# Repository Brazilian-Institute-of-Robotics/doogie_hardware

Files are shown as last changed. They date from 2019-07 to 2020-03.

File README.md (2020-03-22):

# Doogie Hardware
This repository is intend to gather all the files regarding the Doogie Mouse robot hardware and briefly explain about robot's electronic architecture.

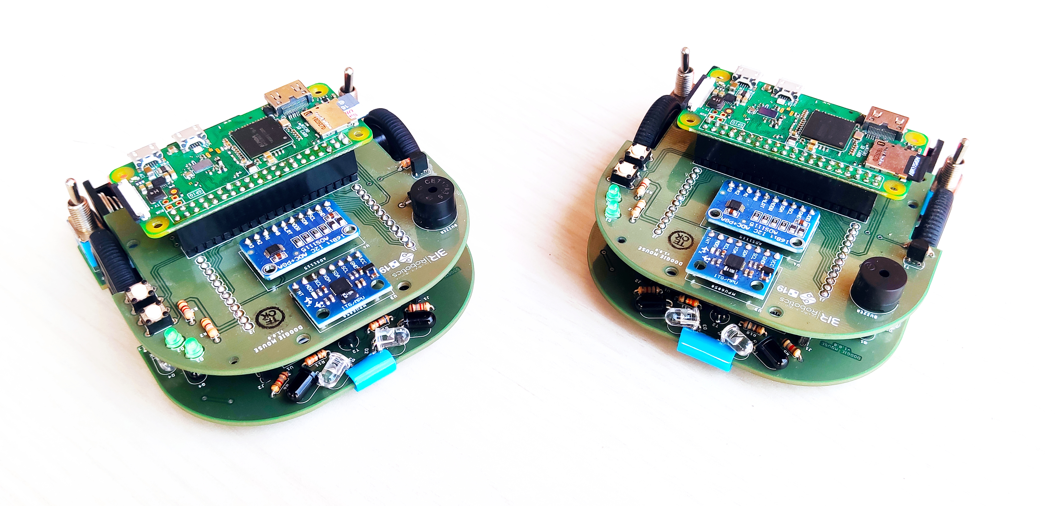
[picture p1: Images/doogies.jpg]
Doogie Photos


## Folder organization
- [Eagle]\: [Autocad Eagle] files (*.sch and *.brd) of top and bottom boards and a file used to check design rules (.dru)
- [Gerbers]\: Files used to manufacture the top and bottom boards
- [Libraries]\: Eagle libraries used in the layout of the Doogie Mouse robot boards
- [Schematics]\: Electronic schematics of top and bottom board in PDF format
- [BOM]\: Bill Of Materials

## Electronic architecture
The electronic architecture in the figure below demonstrates how Doogie Mousee components are electrically interconnected. For the purpose of better visualization, the voltage reference (Ground - GND) was omitted.

<p align="center">
<b>Figure 1: </b>Electronic architecture 
<br>
<br>
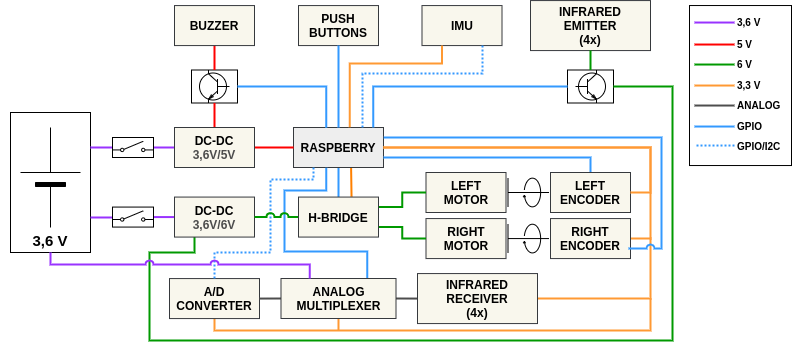
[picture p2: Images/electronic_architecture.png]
Electronic architecture

</p>

The Doogie is equipped with a Li-Ion battery with 3.6 V of nominal voltage. To make the battery voltage level compatible with the other components, two DC-DC converters are used. The first will supply 6 V exclusively for motors and emitting LEDs. The second is responsible for supplying the Raspberry Pi with 5 V. However, the components that are connected to the Raspberry Pi are powered by 3.3 V through an internal DC-DC converter on the microprocessor system board.

In order to facilitate the replication of the robot by users who want to use it, it was decided to use breakout boards, which are pre-assembled electronic boards. Doogie has six of them: two DC-DC voltage converters, an A/D converter, an IMU, an analog multiplexer and an H-Bridge. The other components, such as resistors, transistors, infrared LEDs, phototransistors and connectors, are soldered directly on the PCB.

Doogie components communicate and are controlled in several ways. The A/D converter and the IMU communicate with the Raspberry Pi via an I2C bus. As the specified A/D converter has only 4 channels (one for each infrared sensor), it was decided to use an analog multiplexer to allow the battery voltage value to be obtained as well. This multiplexer is controlled by digital pins from the processing unit. Finally, the control of the motors is performed by an H bridge with two independent channels. This power driver allows the directions of rotation of the motors to be controlled by digital pins from the Raspberry Pi while the speed control is performed by PWM.

For detailed description of components connections, see the electronic schematics [doogie_bottom_board](Schematics/doogie_bottom_board.pdf) and [doogie_top_board](Schematics/doogie_top_board.pdf).

## Boards overview
<p align="center">
<b>Top Board</b>
<br>
<br>
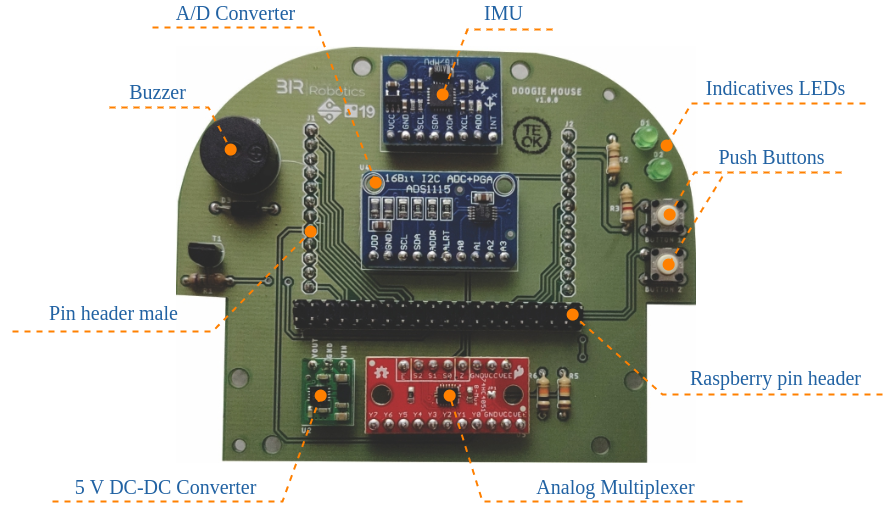
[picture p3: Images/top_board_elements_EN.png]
Top Board Components

</p>

<p align="center">
<b>Bottom Board</b>
<br>
<br>
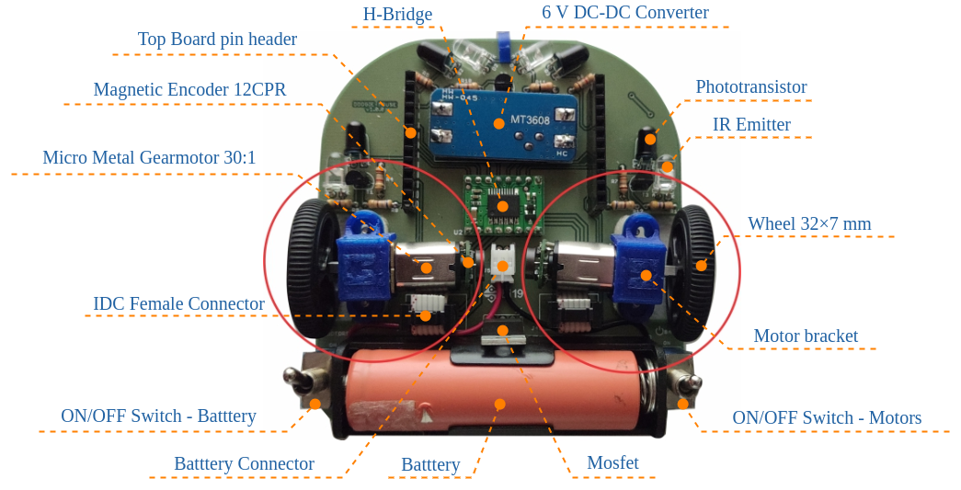
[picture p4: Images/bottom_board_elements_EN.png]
Bottom Board Components

</p>

## Assembly Instructions
See [Hardware Setup] on Doogie wiki page!

## Purpose of the Project

Doogie Mouse platform was originally developed in 2019 as an undergraduate thesis (Theoprax methodoly) at Centro Universitário SENAI CIMATEC in partnership with Brazillian Institute of Robotics, for teaching principles of artificial intelligence using high level framework for writing and reusing robot software.

It's a open source project and expects modifications and contributions from it's users. 

## Change Log
#### [1.0] - 2019-12-10
- First version

## Bugs & Feature Requests
Please report bugs and request features using the [Issue Tracker](https://github.com/Brazilian-Institute-of-Robotics/doogie_hardware/issues).

[Eagle]: https://github.com/Brazilian-Institute-of-Robotics/doogie_hardware/tree/master/Eagle
[Autocad Eagle]: https://www.autodesk.com/products/eagle/overview?geoNavigationPreferredSite=US
[Gerbers]: https://github.com/Brazilian-Institute-of-Robotics/doogie_hardware/tree/master/Gerbers
[Libraries]: https://github.com/Brazilian-Institute-of-Robotics/doogie_hardware/tree/master/Libraries
[Schematics]: https://github.com/Brazilian-Institute-of-Robotics/doogie_hardware/tree/master/Schematics
[BOM]: https://github.com/Brazilian-Institute-of-Robotics/doogie_hardware/tree/master/BOM
[Hardware Setup]: https://github.com/Brazilian-Institute-of-Robotics/doogie/wiki/Hardware-Setup

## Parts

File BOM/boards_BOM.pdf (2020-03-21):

DOOGIE TOP BOARD - BOM

Qty | Value | Device | Package | Parts | Description
2 | | CONN_12 | 1X12 | J1, J2 | Multi connection point. Often used as Generic Header-pin footprint for 0.1 inch spaced/style header connections
2 | 10k | R-EU_0204/7 | 0204/7 | R5, R6 | RESISTOR, European symbol
1 | 1N4004 | 1N4004 | DO41-10 | D3 | DIODE
1 | 390R | R-EU_0204/7 | 0204/7 | R2 | RESISTOR, European symbol
1 | 74HC4051_SPARKFUN | 74HC4051_SPARKFUN | 74HC4051_SPARKFUN | U5
1 | 750R | R-EU_0204/7 | 0204/7 | R1 | RESISTOR, European symbol
1 | 820R | R-EU_0204/7 | 0204/7 | R3 | RESISTOR, European symbol
1 | ADC-4CH-ADS1115 | ADC-4CH-ADS1115 | ADC-4CH-ADS1115 | U4 | 4 Channel 16-Bit Analog-to-Digital Converter based on ADS1115 chip
1 | BC337 | BC337 | TO92 | T1 | NPN TRANSISTOR
1 | F/TMB | F/TMB | F/TMB | BUZZER | BUZZER Source: Buerklin
2 | GREEN | LED3MM | LED_3MM | D1, D2 | LED (Generic)
1 | GY-521MPU6050 | GY-521MPU6050 | GY-521 | U3
2MOMENTARY-SWITCH-SPST-PTH-6.0MM MOMENTARY-SWITCH-SPST-PTH-6.0MM TACTILE_SWITCH_PTH_6.0MM | | | | S1, S2 | Momentary Switch (Pushbutton) - SPST
1 | RPI-ZERO | RPI-ZERO | | U1
1 | U1V10F5 | U1V10F5 | U1V10F5 | U2 | Pololu 5V Step-Up Voltage Regulator U1V10F5

DOOGIE BOTTOM BOARD - BOM

Qty | Value | Device | Package | Parts | Description
1 | | CONN_02JST-PTH-2 | JST-2-PTH | J5 | Multi connection point. Often used as Generic Header-pin footprint for 0.1 inch spaced/style header connections
2 | | CONN_03X2SHROUD | 2X3-SHROUDED | J3, J4 | Multi connection point. Often used as Generic Header-pin footprint for 0.1 inch spaced/style header connections
2 | | CONN_12 | 1X12 | J1, J2 | Multi connection point. Often used as Generic Header-pin footprint for 0.1 inch spaced/style header connections
2 | | M9040P | M9040P | S1, S2 | TOGGLE SWITCH
4 | 1k8 | R-EU_0204/7 | 0204/7 | R4, R5, R6, R7 | RESISTOR, European symbol
1 | 33R | R-EU_0204/7 | 0204/7 | R11 | RESISTOR, European symbol
2 | 47R | R-EU_0204/7 | 0204/7 | R9, R13 | RESISTOR, European symbol
3 | 680R | R-EU_0204/7 | 0204/7 | R8, R10, R12 | RESISTOR, European symbol
1 | BATTERY_HOLDER | BATTERY_HOLDER | BATTERY_HOLDER | BATTERY_HOLDER
3 | BC337 | BC337 | TO92 | T1, T2, T3 | NPN TRANSISTOR
1 | DC-DC-STEP-UP-MT3608 | DC-DC-STEP-UP-MT3608 | DC-DC-STEP-UP-MT3608 | U1 | DC/DC Step-Up Regulator based on MT3608 chip
1 | IRF9530 | IRF9530 | TO220BV | Q6 | P-CHANNEL HEXFET POWER-MOS-FET
4 | SFH4545 | SFH4545 | SFH4545-AK | D1, D2, D3, D4
1 | TB6612FNG | TB6612FNG | TB6612FNG | U2 | TB6612FNG Dual Motor Driver Carrier
4 | TEFT4300 | TEFT4300_5MM_RA | TEFT_5MM_RA | Q1, Q2, Q3, Q4 | TEFT4300

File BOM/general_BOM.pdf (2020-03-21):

Top Board
Item | Component | Qty. | Description
1 | Printed Circuit Board | 1 | doogie_top_board
2 | Raspberry Pi | 1 | Raspberry Pi Zero W
3 | Micro Sd | 1 | Memory Card microSD 16GB Class 10 SanDisk
4 | Voltage Regulator | 1 | 5V voltage regulator Pololu Step-Up U1V10F5
5 | Imu | 1 | 3 axes accelerometer and gyro 6-DOF MPU 6050
6 | A / D Converter | 1 | Analog Digital Converter channels 4 ADS1115
7 | Analog Multiplexer | 1 | Module Multiplexers 74HC4051 8 channels Sparkfun
8 | Pin Male Bar 1X12 | 1 | Pin bar 1×40 180º 20mm
9 | Pin Bar Male 2X40 | 1 | Pin bar 2×40 180º
10 | Pin Female Bar 2X20 | 1 | Pin Bar 2 × 20 Male And Female
10 | Push Button | 2 | Key Touch Push-Button
11 | Led | 2 | 3mm LEDs
12 | Buzzer | 1 | Active buzzer 5V
13 | Transistor | 1 | NPN transistor BC337
14 | Diode | 1 | Rectifier diode 1N4007
15 | Resistor | 1 | Resistor 750Ω 1 / 4W
16 | Resistor | 1 | Resistor 390Ω 1 / 4W
17 | Resistor | 1 | Resistor 820Ω 1 / 4W
18 | Resistor | 2 | Resistor 10k 1 / 4W

Bottom Board
Item | Component | Qty. | Description
1 | Printed Circuit Board | 1 | doogie_bottom_board
2 | Voltage Regulator | 1 | Boost Converter DC Adjustable Step Up
3 | H Bridge | 1 | TB6612FNG Dual Motor Driver Carrier
4 | Pin Female Bar 1X12 | 1 | Pins bar 1 × 40 Female 180º
5 | Pin Male Bar 2X3 | 2 | Pin bar 180º 2 x 40 (used on the board top)
6 | Connector | 1 | Connector JST XH male wrapped
7 | 3 Terminals Switch | 2 | Switch 3 Terminals Toggle Switch SPDT
8 | Phototransistor | 4 | Infrared Phototransistor 5mm IR receiver
9 | Infrared Emitter | 4 | Infrared IR transmitter LED 5mm
10 | Transistor | 3 | NPN transistor BC337
11 | Mosfet | 1 | P-Channel MOSFET TO220 IRF4905
12 | Resistor | 1 | Resistor 33Ω 1 / 4W
13 | Resistor | 2 | Resistor 47Ω 1 / 4W
14 | Resistor | 3 | Resistor 680Ω 1 / 4W
15 | Resistor | 4 | Resistor 1k8Ω 1 / 4W
16 | Motor | 2 | 30: 1 Micro Metal Gearmotor HP 6V motor shaft extended
17 | Pair Of Magnetic Encoder | 1 | Pair of magnetic metal micro motor encoder Gearmotors, 12 CPR 2.7-18V
18 | Pair Of Wheels | 1 | Pololu wheel pair 32 × 7mm
19 | Par Motor Brackets | 1 | Motor Bracket - 3D Printing
20 | IDC Female connector | 2 | IDC female connector - 6-way
21 | Flat Cable | 1 | Flat Cable - 6 parts (1m)
22 | Battery | 1 | Li-Ion 18650 3.7V 2200mAh 2C
23 | Support For Battery | 1 | Support for battery 18650

Auxiliaries
Item | Component | Qty. | Description
1 | USB/Micro USB Adapter | 2 | Cable USB to Micro USB
2 | HDMI/Mini HDMI Adapter | 1 | HDMI Female Adapter Mini HDMI Male

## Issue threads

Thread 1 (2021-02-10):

Fix small errors on the board first version

mateusmenezes95, 2021-02-10:
After the assembly and test with the first version of the doogie boards, some points were listed to be fixed in the next versions. Below are the point with some comments.

- **Inverter DC-DC of the motors:** In the assembly process of the bottom board, it was noticed the pads of the motors' DC-DC converter were inverted. The solution was to put the DC-DC head down. Then it's necessary to fix this issue in the next versions.
- **Drill the key holes:** It's necessary to increase the diameter of ON/OFF key holes pads because in the first version the diameter no fit with the key pins.
- **Reverse silk ON / OFF of the ON/OFF keys:** In the current verison putting the key lever on OFF position turn on the robot and putting in ON position, turn off. This issue could be solved just by inverting the silk on the bottom board.
- **Place the silk on the power LEDs:** The top board has two LEDs to indicate when power and the logical circuit are turned on. However, there is no indication on the board to inform which LED is related to the power circuit and which LED is related to the logical circuit.
- **Put I2C address in ADS1115 (Connect ADDR in GND):** It's necessary to connect the ADDR pin of ADS1115 to GND to assign it an I2C address. In the current version, this connection was made by wire.
- **Place test points:** For hardware debug purposes it's nice to put point test points on the boards to evaluate voltage levels and signal. It's a good practice in PCB development.
- **Increase the space where the wheels are by 2mm:** It's necessary to increase the space where the wheels are to avoid the tires touch on the board edges.
- **Place capacitors in parallel with the emitters for the use of current peaks:** Put the capacitor to provide high peak current in small intervals. With this approach, the resolution of the sensor is improved. This a common technique used in micromouse robots.
- **Change Buzzer's GPIO:** The buzzer it's not working well because like seems the pin used to control it is connected with another function in the board. It's important to do tests before choose a new pin.
- **Connect the interruption pin of the MPU6050:** It's nice to connect the interruption pin of the IMU to one pin of the raspberry to enjoy the interruption functionalities of the MPU6050 device.

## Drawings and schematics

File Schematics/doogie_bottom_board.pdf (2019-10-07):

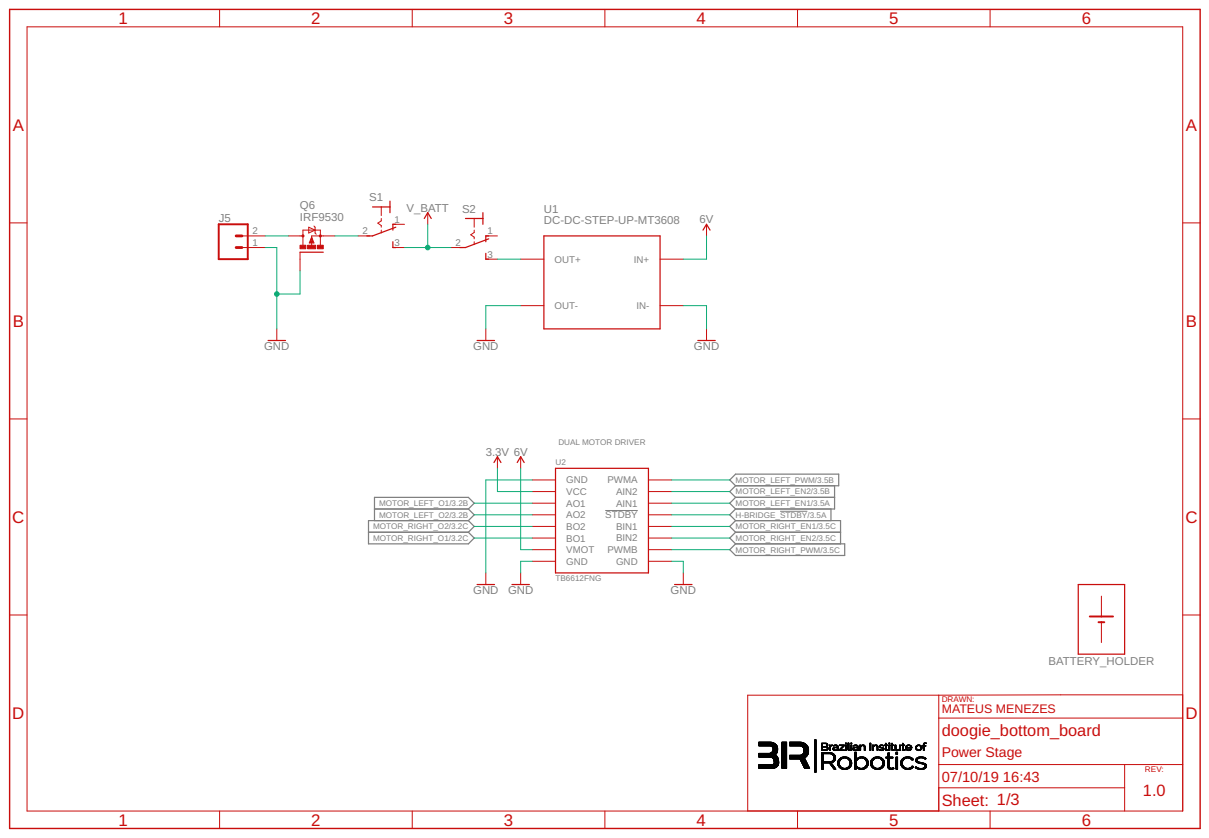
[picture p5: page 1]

DC-DC-STEP-UP-MT3608

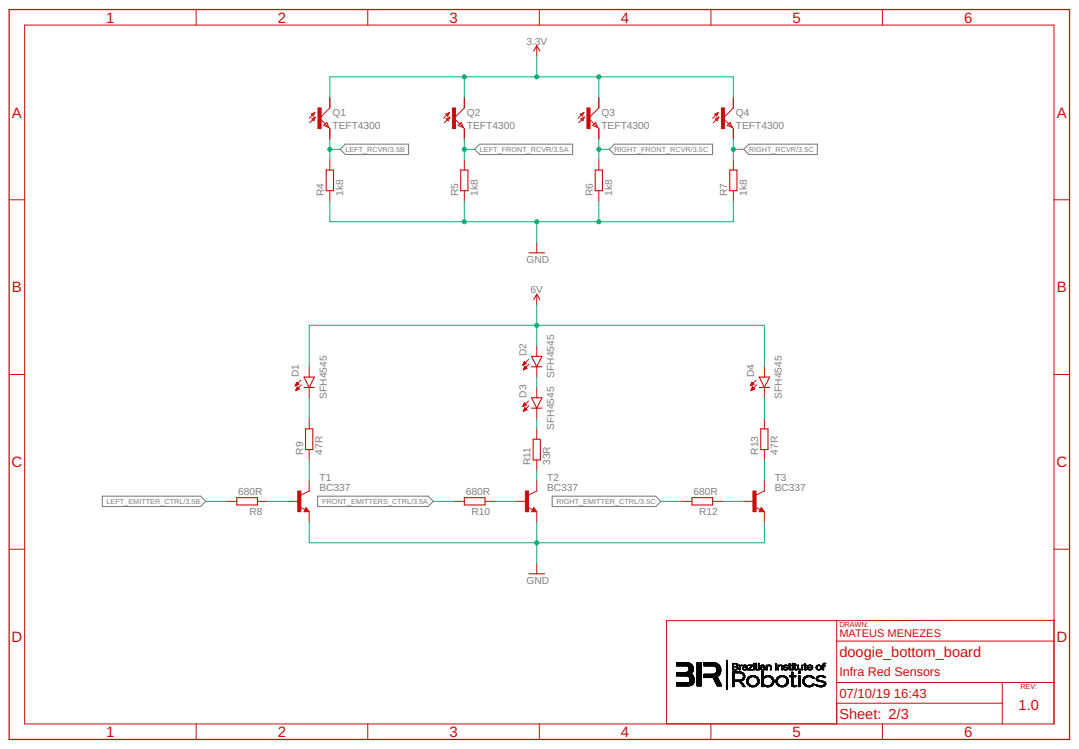
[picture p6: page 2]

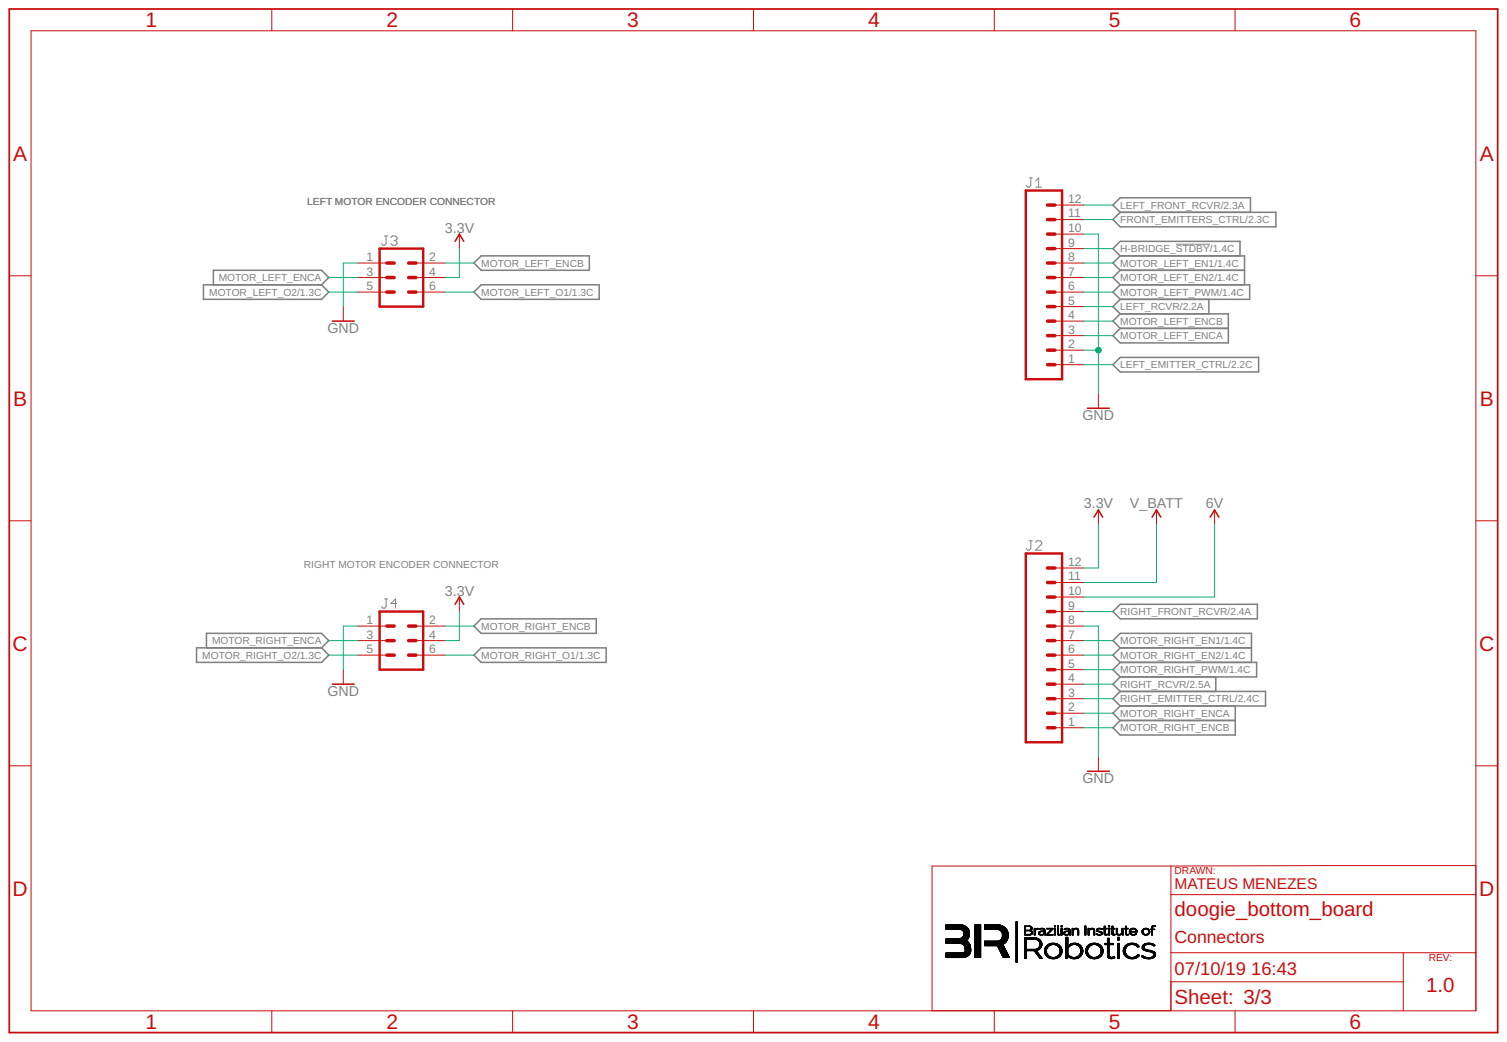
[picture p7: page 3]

LEFT MOTOR ENCODER CONNECTOR

LEFT MOTOR ENCODER CONNECTOR 3.3V

RIGHT MOTOR ENCODER CONNECTOR

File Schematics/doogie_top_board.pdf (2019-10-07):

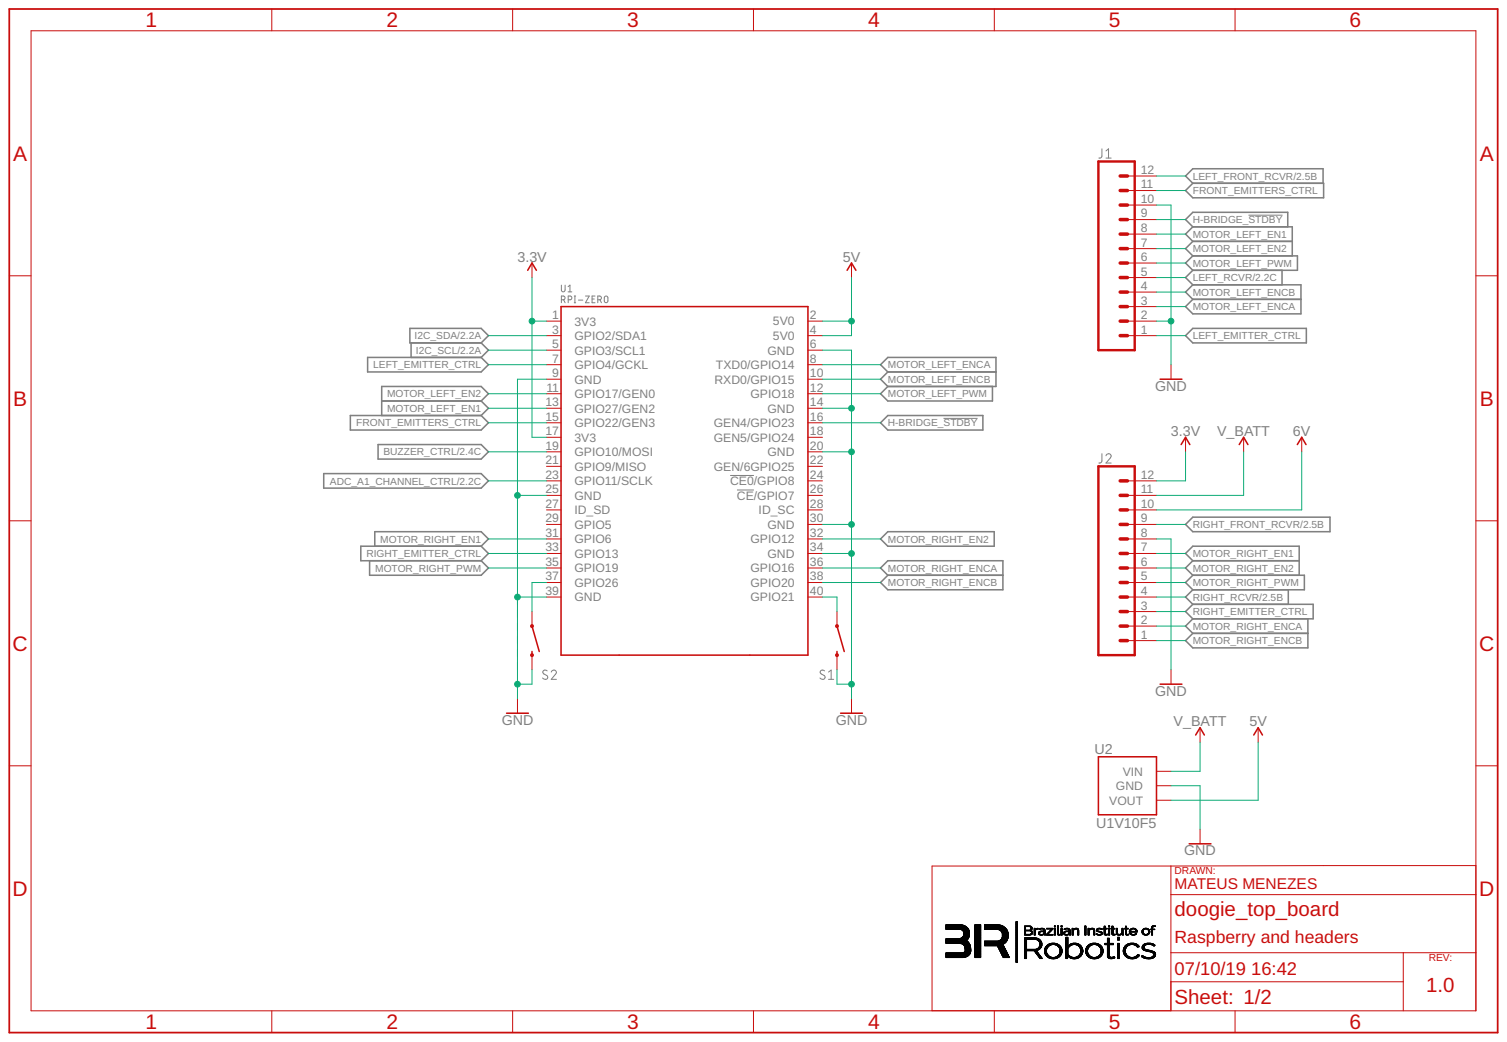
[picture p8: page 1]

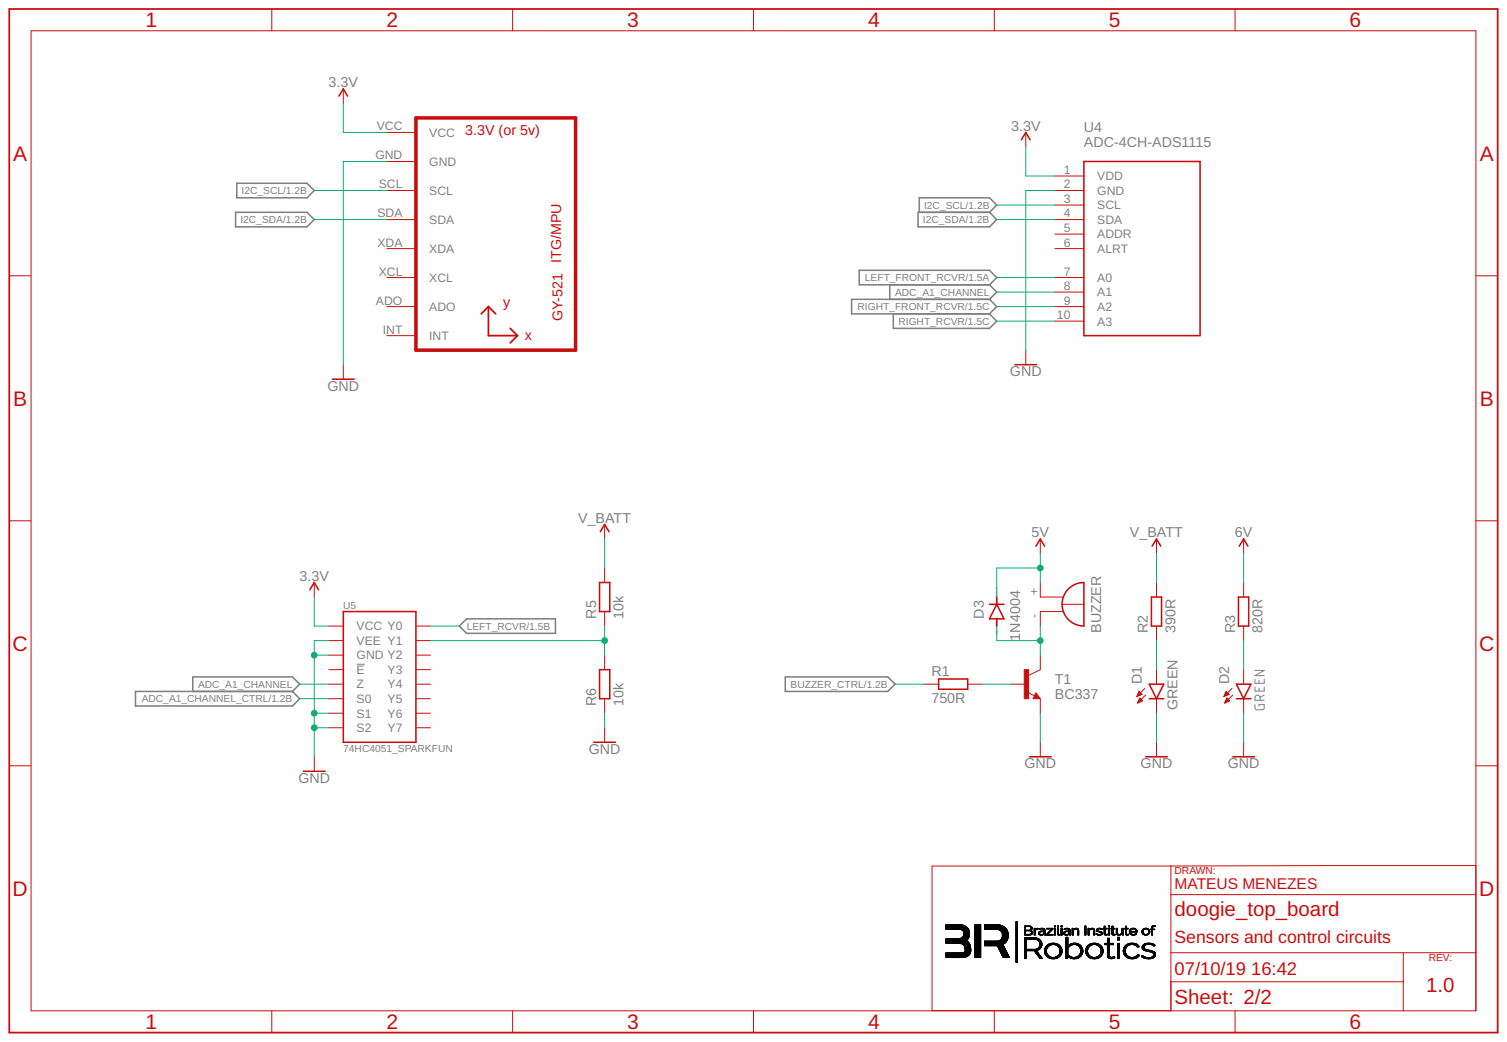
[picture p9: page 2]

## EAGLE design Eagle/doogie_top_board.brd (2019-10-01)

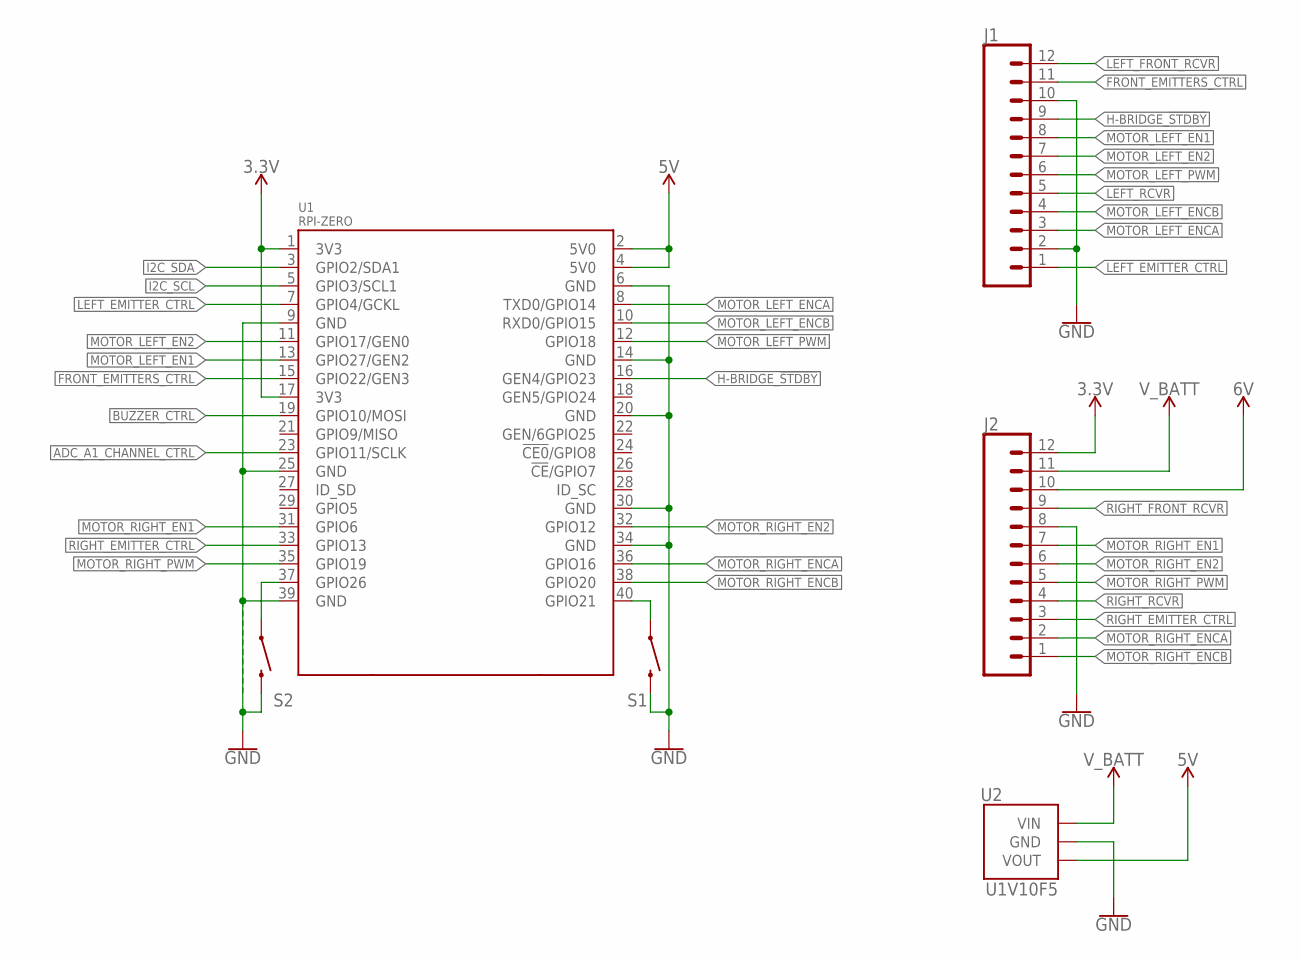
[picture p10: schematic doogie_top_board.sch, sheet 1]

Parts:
J1, J2: CONN_12; 1X12
S1, S2: MOMENTARY-SWITCH-SPST-PTH-6.0MM; TACTILE_SWITCH_PTH_6.0MM
U1: RPI-ZERO; RASPBERRYPI_BASTELSTUBE_V13_RASPI_BOARD_B+_FULL
U2: U1V10F5

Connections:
3.3V: J2.12, U1.1 (3V3), U1.17 (3V3); also elsewhere on the board
5V: U1.2 (5V0), U1.4 (5V0), U2.VOUT; also elsewhere on the board
ADC_A1_CHANNEL_CTRL: U1.23 (GPIO11/SCLK); also elsewhere on the board
BUZZER_CTRL: U1.19 (GPIO10/MOSI); also elsewhere on the board
FRONT_EMITTERS_CTRL: J1.11, U1.15 (GPIO22/GEN3)
GND: J1.2, J1.10, J2.8, S1.3 (2), S2.3 (2), U1.6 (GND), U1.9 (GND), U1.14 (GND), U1.20 (GND), U1.25 (GND), U1.30 (GND), U1.34 (GND), U1.39 (GND), U2.GND; also elsewhere on the board
H-BRIDGE_!STDBY: J1.9, U1.16 (GEN4/GPIO23)
I2C_SCL: U1.5 (GPIO3/SCL1); also elsewhere on the board
I2C_SDA: U1.3 (GPIO2/SDA1); also elsewhere on the board
LEFT_EMITTER_CTRL: J1.1, U1.7 (GPIO4/GCKL)
LEFT_FRONT_RCVR: J1.12; also elsewhere on the board
LEFT_RCVR: J1.5; also elsewhere on the board
MOTOR_LEFT_EN1: J1.8, U1.13 (GPIO27/GEN2)
MOTOR_LEFT_EN2: J1.7, U1.11 (GPIO17/GEN0)
MOTOR_LEFT_ENCA: J1.3, U1.8 (TXD0/GPIO14)
MOTOR_LEFT_ENCB: J1.4, U1.10 (RXD0/GPIO15)
MOTOR_LEFT_PWM: J1.6, U1.12 (GPIO18)
MOTOR_RIGHT_EN1: J2.7, U1.31 (GPIO6)
MOTOR_RIGHT_EN2: J2.6, U1.32 (GPIO12)
MOTOR_RIGHT_ENCA: J2.2, U1.36 (GPIO16)
MOTOR_RIGHT_ENCB: J2.1, U1.38 (GPIO20)
MOTOR_RIGHT_PWM: J2.5, U1.35 (GPIO19)
unnamed: S2.1, U1.37 (GPIO26)
unnamed: S1.1, U1.40 (GPIO21)
RIGHT_EMITTER_CTRL: J2.3, U1.33 (GPIO13)
RIGHT_FRONT_RCVR: J2.9; also elsewhere on the board
RIGHT_RCVR: J2.4; also elsewhere on the board
VOUT: J2.10; also elsewhere on the board
V_BATT: J2.11, U2.VIN; also elsewhere on the board

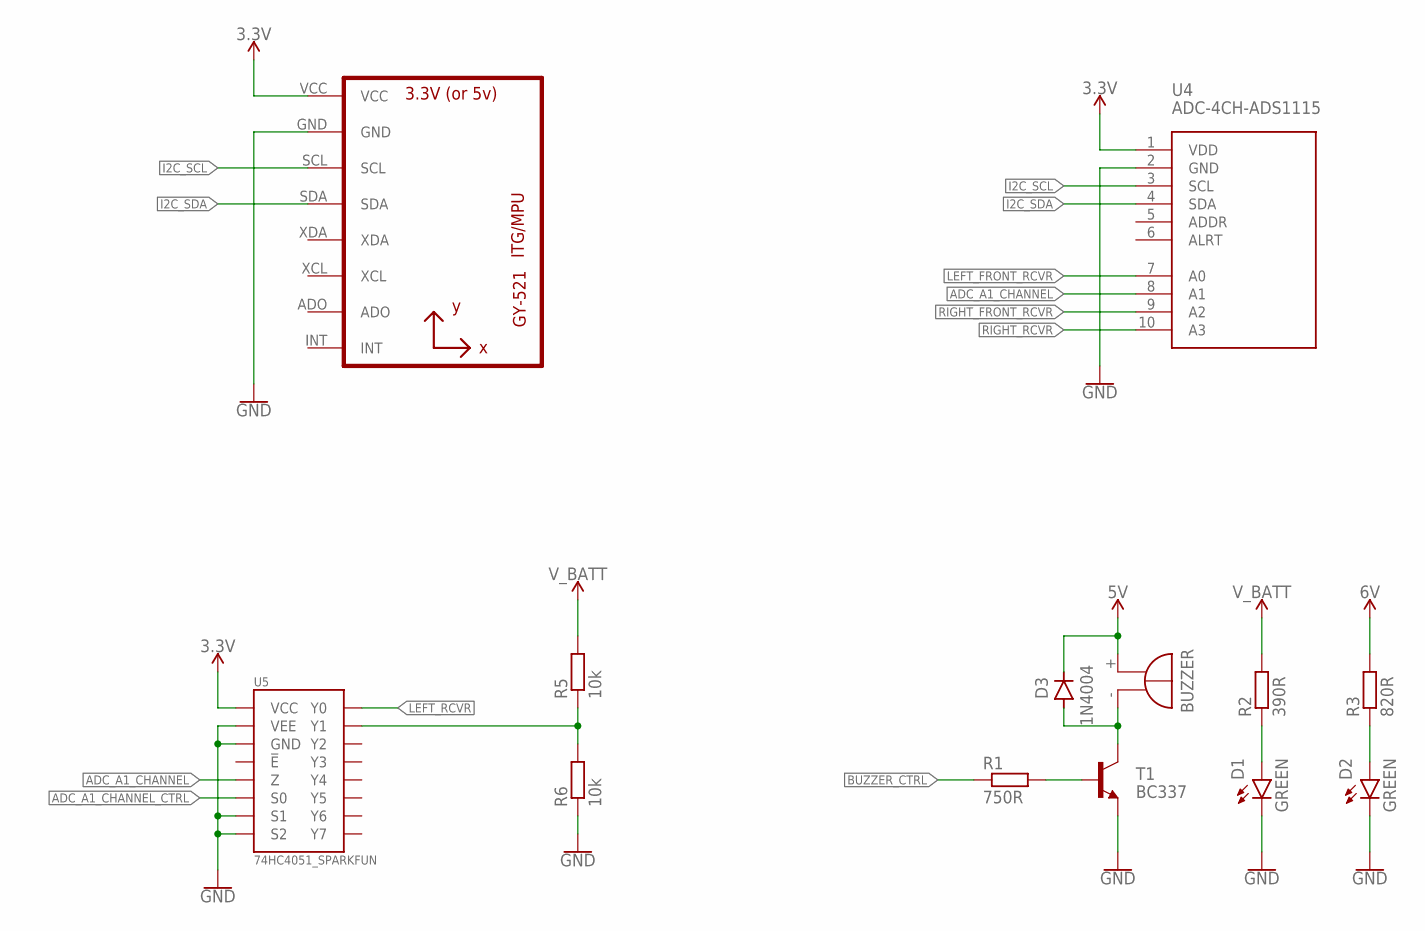
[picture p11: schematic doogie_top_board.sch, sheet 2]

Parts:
BUZZER: F/TMB
D1, D2: GREEN; LED_3MM
D3: 1N4004; DO41-10
R1: 750R; 0204/7
R2: 390R; 0204/7
R3: 820R; 0204/7
R5, R6: 10k; 0204/7
T1: BC337; TO92
U3: GY-521MPU6050; GY-521
U4: ADC-4CH-ADS1115
U5: 74HC4051_SPARKFUN

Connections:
3.3V: U3.VCC, U4.1 (VDD), U5.VCC, U5.VCC@1 (VCC); also elsewhere on the board
5V: BUZZER.+, D3.C; also elsewhere on the board
ADC_A1_CHANNEL: U4.8 (A1), U5.Z
ADC_A1_CHANNEL_CTRL: U5.S0; also elsewhere on the board
BUZZER_CTRL: R1.1; also elsewhere on the board
GND: D1.K (C), D2.K (C), R6.1, T1.1 (E), U3.GND, U4.2 (GND), U5.GND, U5.GND@1 (GND), U5.S1, U5.S2, U5.VEE, U5.VEE@1 (VEE); also elsewhere on the board
I2C_SCL: U3.SCL, U4.3 (SCL); also elsewhere on the board
I2C_SDA: U3.SDA, U4.4 (SDA); also elsewhere on the board
LEFT_FRONT_RCVR: U4.7 (A0); also elsewhere on the board
LEFT_RCVR: U5.Y0; also elsewhere on the board
unnamed: BUZZER.-, D3.A, T1.3 (C)
unnamed: R1.2, T1.2 (B)
unnamed: D1.A, R2.1
unnamed: D2.A, R3.1
unnamed: R5.1, R6.2, U5.Y1
RIGHT_FRONT_RCVR: U4.9 (A2); also elsewhere on the board
RIGHT_RCVR: U4.10 (A3); also elsewhere on the board
VOUT: R3.2; also elsewhere on the board
V_BATT: R2.2, R5.2; also elsewhere on the board

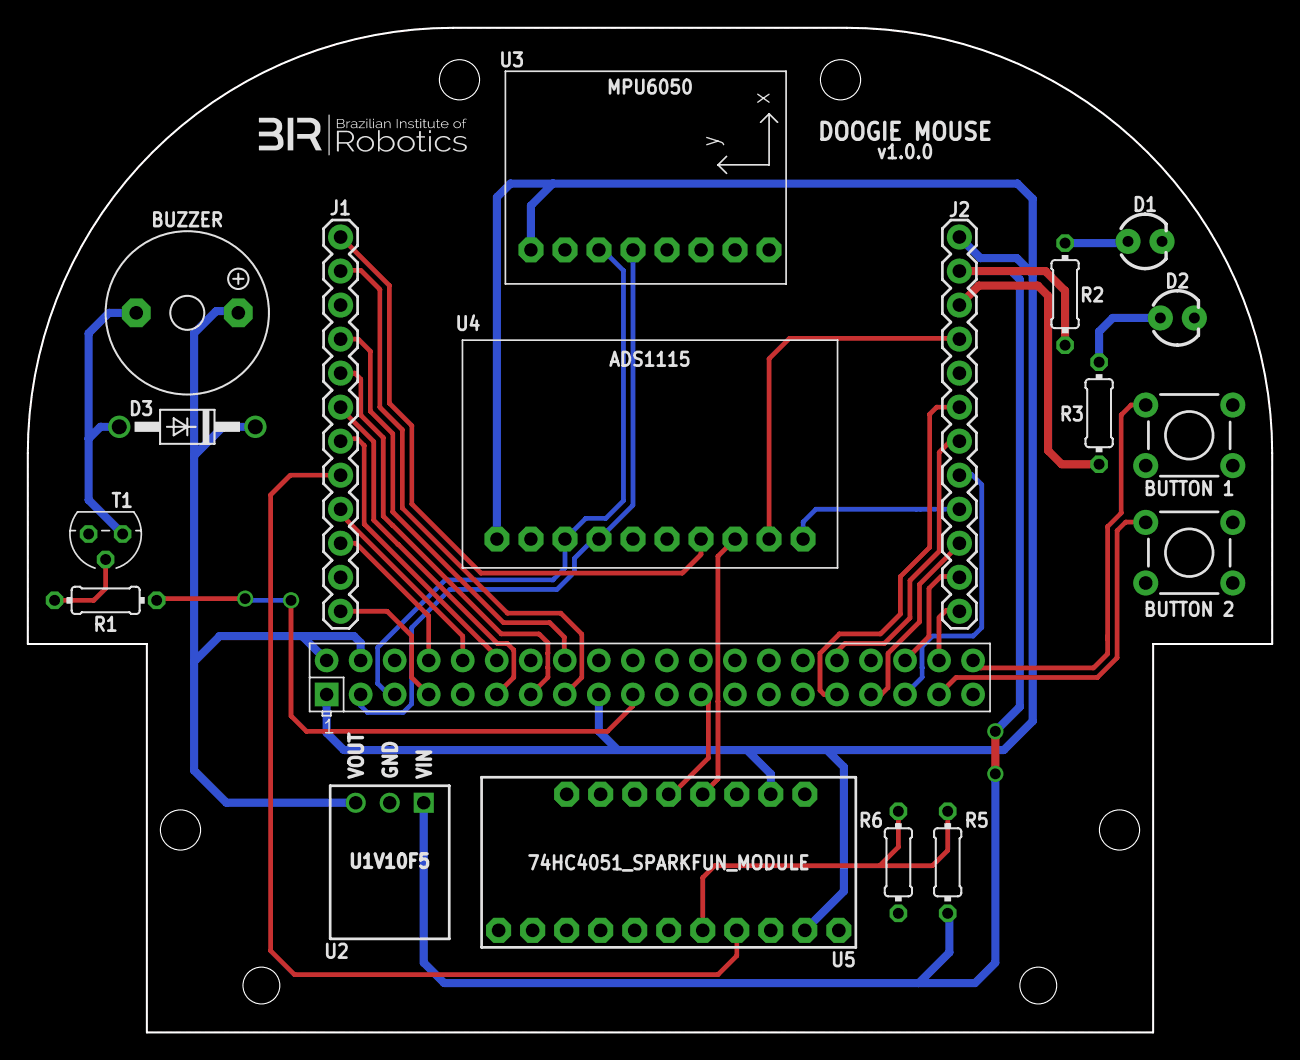
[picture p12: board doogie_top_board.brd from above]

Board: 2 copper layers, 92.9 x 75.0 mm, 19 parts (0 on the bottom side), 35 nets.

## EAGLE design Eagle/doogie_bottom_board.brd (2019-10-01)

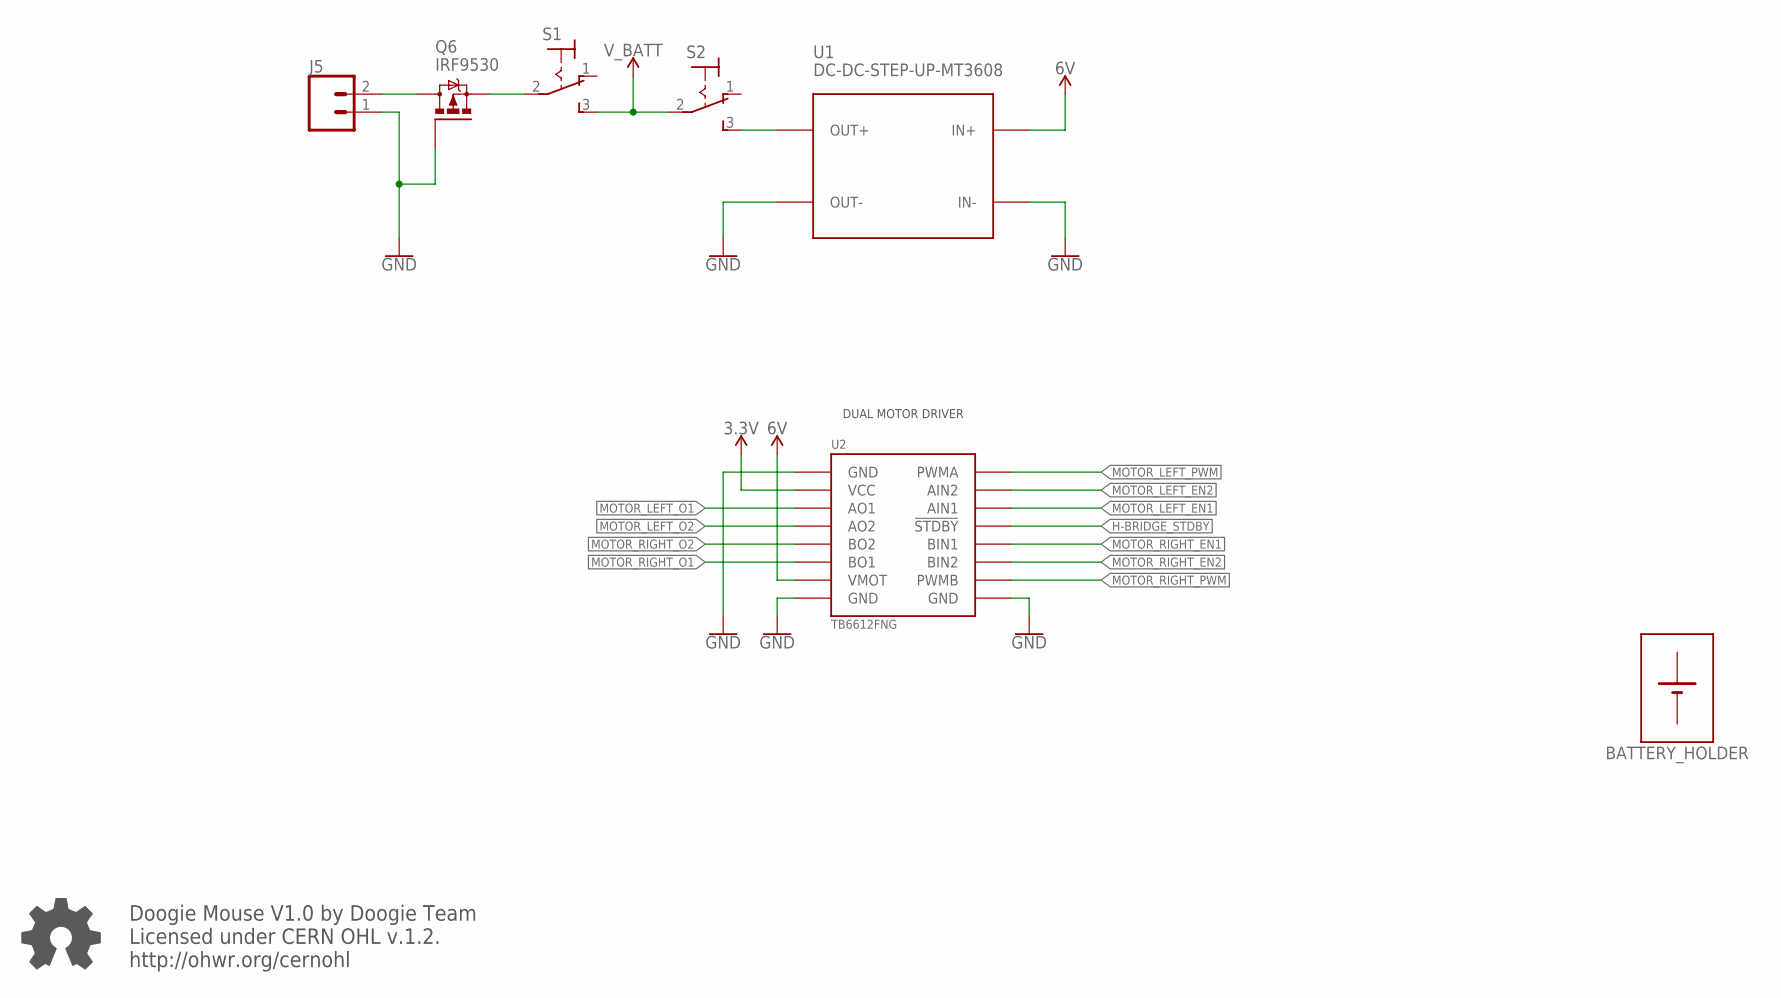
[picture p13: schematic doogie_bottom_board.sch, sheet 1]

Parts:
BATTERY_HOLDER: BATTERY_HOLDER
J5: CONN_02JST-PTH-2; JST-2-PTH
Q6: IRF9530; TO220BV
S1, S2: M9040P
U1: DC-DC-STEP-UP-MT3608
U2: TB6612FNG

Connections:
3.3V: U2.2 (VCC); also elsewhere on the board
6V: U1.IN+, U2.7 (VMOT); also elsewhere on the board
FILLING_POLYGON: J5.1, Q6.G, U1.IN-, U1.OUT-, U2.1 (GND), U2.8 (GND), U2.16 (GND); also elsewhere on the board
H-BRIDGE_!STDBY: U2.12 (!STDBY!); also elsewhere on the board
MOTOR_LEFT_EN1: U2.11 (AIN1); also elsewhere on the board
MOTOR_LEFT_EN2: U2.10 (AIN2); also elsewhere on the board
MOTOR_LEFT_O1: U2.3 (AO1); also elsewhere on the board
MOTOR_LEFT_O2: U2.4 (AO2); also elsewhere on the board
MOTOR_LEFT_PWM: U2.9 (PWMA); also elsewhere on the board
MOTOR_RIGHT_EN1: U2.13 (BIN1); also elsewhere on the board
MOTOR_RIGHT_EN2: U2.14 (BIN2); also elsewhere on the board
MOTOR_RIGHT_O1: U2.6 (BO1); also elsewhere on the board
MOTOR_RIGHT_O2: U2.5 (BO2); also elsewhere on the board
MOTOR_RIGHT_PWM: U2.15 (PWMB); also elsewhere on the board
unnamed: S2.3 (S), U1.OUT+
unnamed: J5.2, Q6.D
unnamed: Q6.S, S1.2
V_BATT: S1.3 (S), S2.2; also elsewhere on the board

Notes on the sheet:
Doogie Mouse V1.0 by Doogie Team Licensed under CERN OHL v.1.2. http://ohwr.org/cernohl
DUAL MOTOR DRIVER

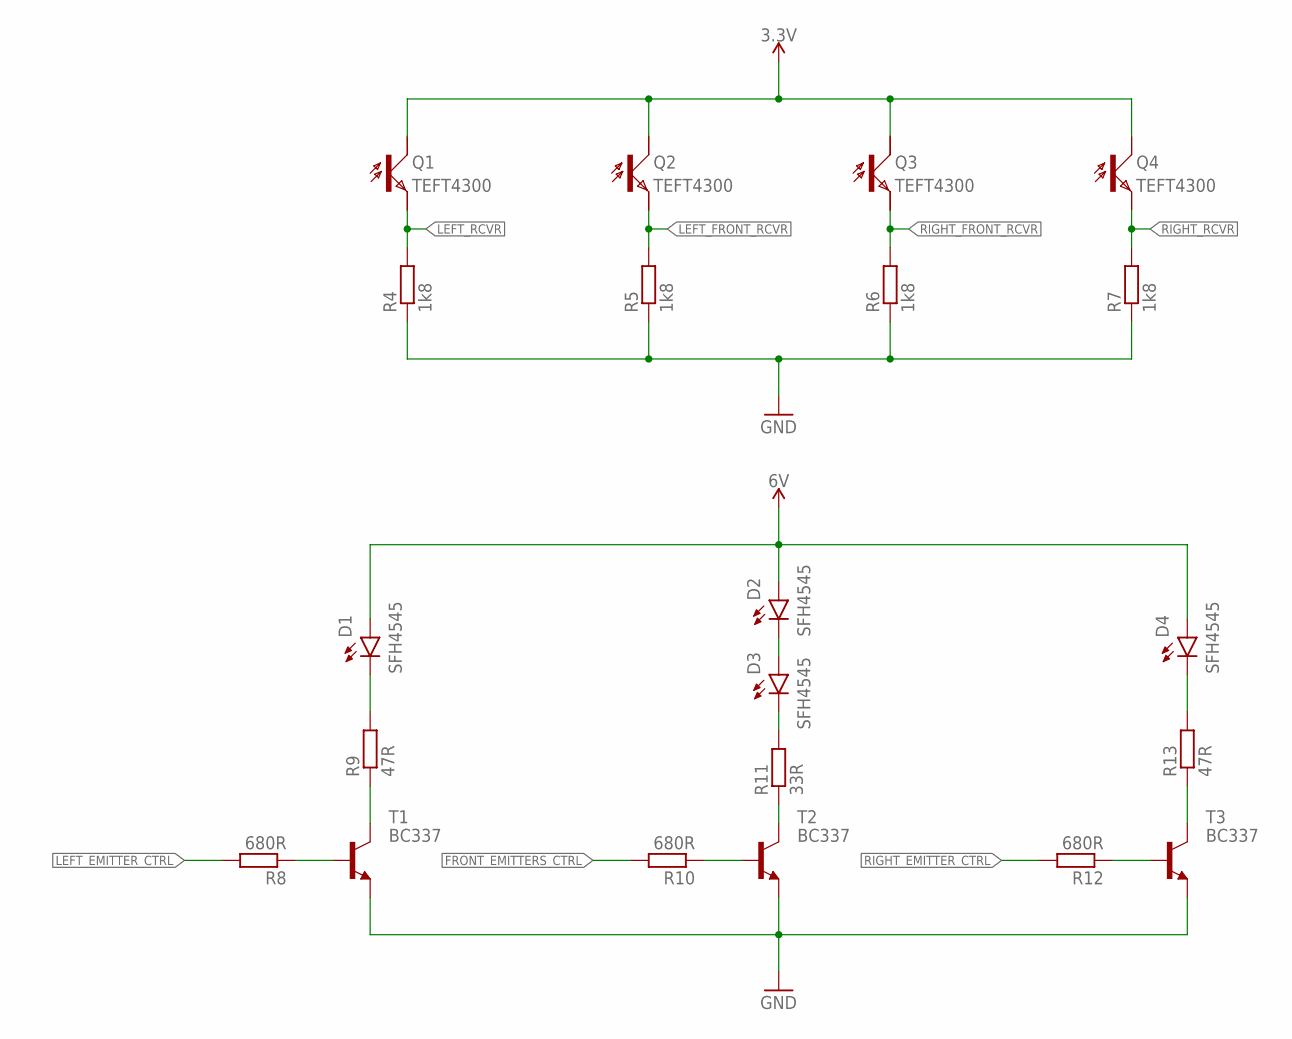
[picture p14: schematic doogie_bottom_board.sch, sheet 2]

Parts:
D1, D2, D3, D4: SFH4545; SFH4545-AK
Q1, Q2, Q3, Q4: TEFT4300; TEFT_5MM_RA
R4, R5, R6, R7: 1k8; 0204/7
R8, R10, R12: 680R; 0204/7
R9, R13: 47R; 0204/7
R11: 33R; 0204/7
T1, T2, T3: BC337; TO92

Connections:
3.3V: Q1.C, Q2.C, Q3.C, Q4.C; also elsewhere on the board
6V: D1.A, D2.A, D4.A; also elsewhere on the board
FILLING_POLYGON: R4.1, R5.1, R6.1, R7.1, T1.1 (E), T2.1 (E), T3.1 (E); also elsewhere on the board
FRONT_EMITTERS_CTRL: R10.2; also elsewhere on the board
LEFT_EMITTER_CTRL: R8.2; also elsewhere on the board
LEFT_FRONT_RCVR: Q2.E, R5.2; also elsewhere on the board
LEFT_RCVR: Q1.E, R4.2; also elsewhere on the board
unnamed: R9.1, T1.3 (C)
unnamed: R11.1, T2.3 (C)
unnamed: R13.1, T3.3 (C)
unnamed: R8.1, T1.2 (B)
unnamed: R10.1, T2.2 (B)
unnamed: R12.1, T3.2 (B)
unnamed: D2.K (C), D3.A
unnamed: D1.K (C), R9.2
unnamed: D4.K (C), R13.2
unnamed: D3.K (C), R11.2
RIGHT_EMITTER_CTRL: R12.2; also elsewhere on the board
RIGHT_FRONT_RCVR: Q3.E, R6.2; also elsewhere on the board
RIGHT_RCVR: Q4.E, R7.2; also elsewhere on the board

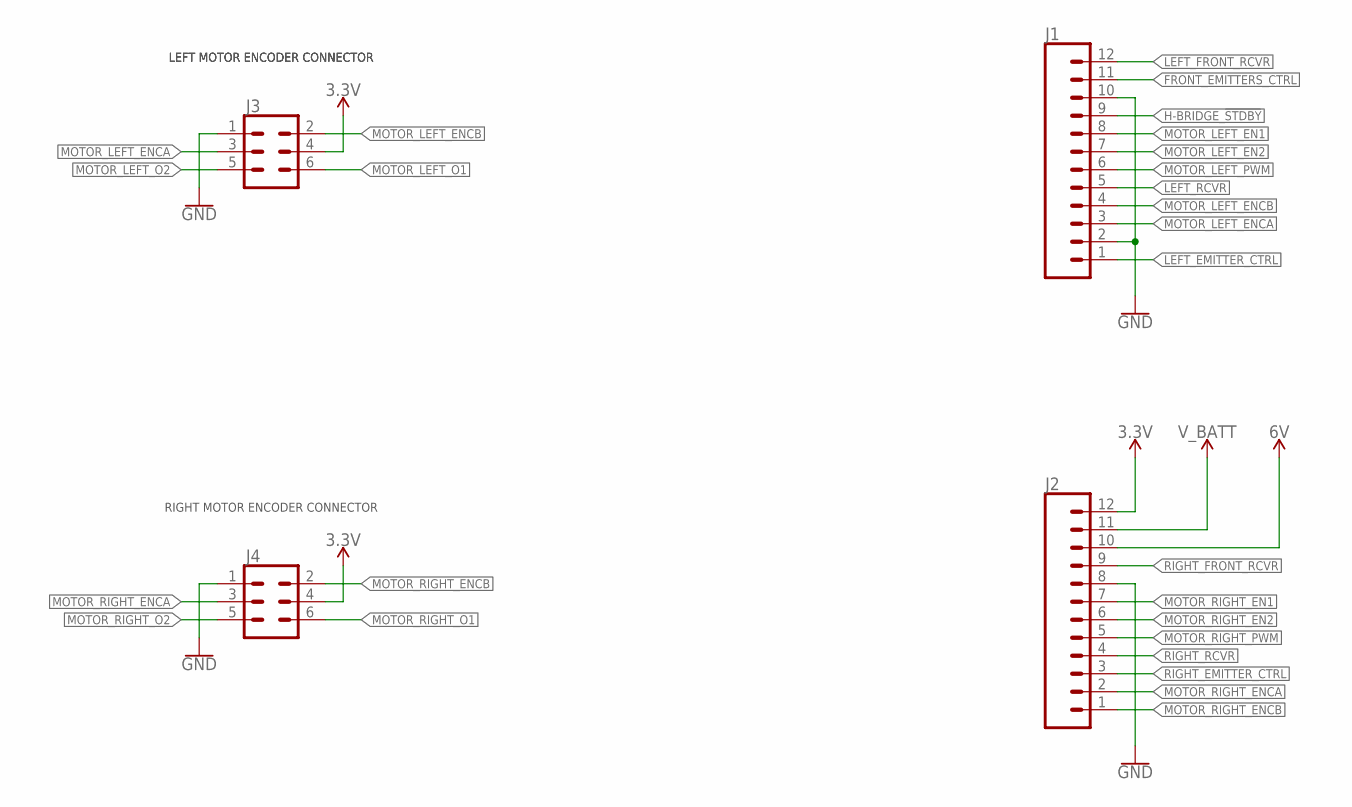
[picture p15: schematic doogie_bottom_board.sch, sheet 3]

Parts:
J1, J2: CONN_12; 1X12
J3, J4: CONN_03X2SHROUD; 2X3-SHROUDED

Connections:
3.3V: J2.12, J3.4, J4.4; also elsewhere on the board
6V: J2.10; also elsewhere on the board
FILLING_POLYGON: J1.2, J1.10, J2.8, J3.1, J4.1; also elsewhere on the board
FRONT_EMITTERS_CTRL: J1.11; also elsewhere on the board
H-BRIDGE_!STDBY: J1.9; also elsewhere on the board
LEFT_EMITTER_CTRL: J1.1; also elsewhere on the board
LEFT_FRONT_RCVR: J1.12; also elsewhere on the board
LEFT_RCVR: J1.5; also elsewhere on the board
MOTOR_LEFT_EN1: J1.8; also elsewhere on the board
MOTOR_LEFT_EN2: J1.7; also elsewhere on the board
MOTOR_LEFT_ENCA: J1.3, J3.3
MOTOR_LEFT_ENCB: J1.4, J3.2
MOTOR_LEFT_O1: J3.6; also elsewhere on the board
MOTOR_LEFT_O2: J3.5; also elsewhere on the board
MOTOR_LEFT_PWM: J1.6; also elsewhere on the board
MOTOR_RIGHT_EN1: J2.7; also elsewhere on the board
MOTOR_RIGHT_EN2: J2.6; also elsewhere on the board
MOTOR_RIGHT_ENCA: J2.2, J4.3
MOTOR_RIGHT_ENCB: J2.1, J4.2
MOTOR_RIGHT_O1: J4.6; also elsewhere on the board
MOTOR_RIGHT_O2: J4.5; also elsewhere on the board
MOTOR_RIGHT_PWM: J2.5; also elsewhere on the board
RIGHT_EMITTER_CTRL: J2.3; also elsewhere on the board
RIGHT_FRONT_RCVR: J2.9; also elsewhere on the board
RIGHT_RCVR: J2.4; also elsewhere on the board
V_BATT: J2.11; also elsewhere on the board

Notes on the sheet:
LEFT MOTOR ENCODER CONNECTOR
RIGHT MOTOR ENCODER CONNECTOR

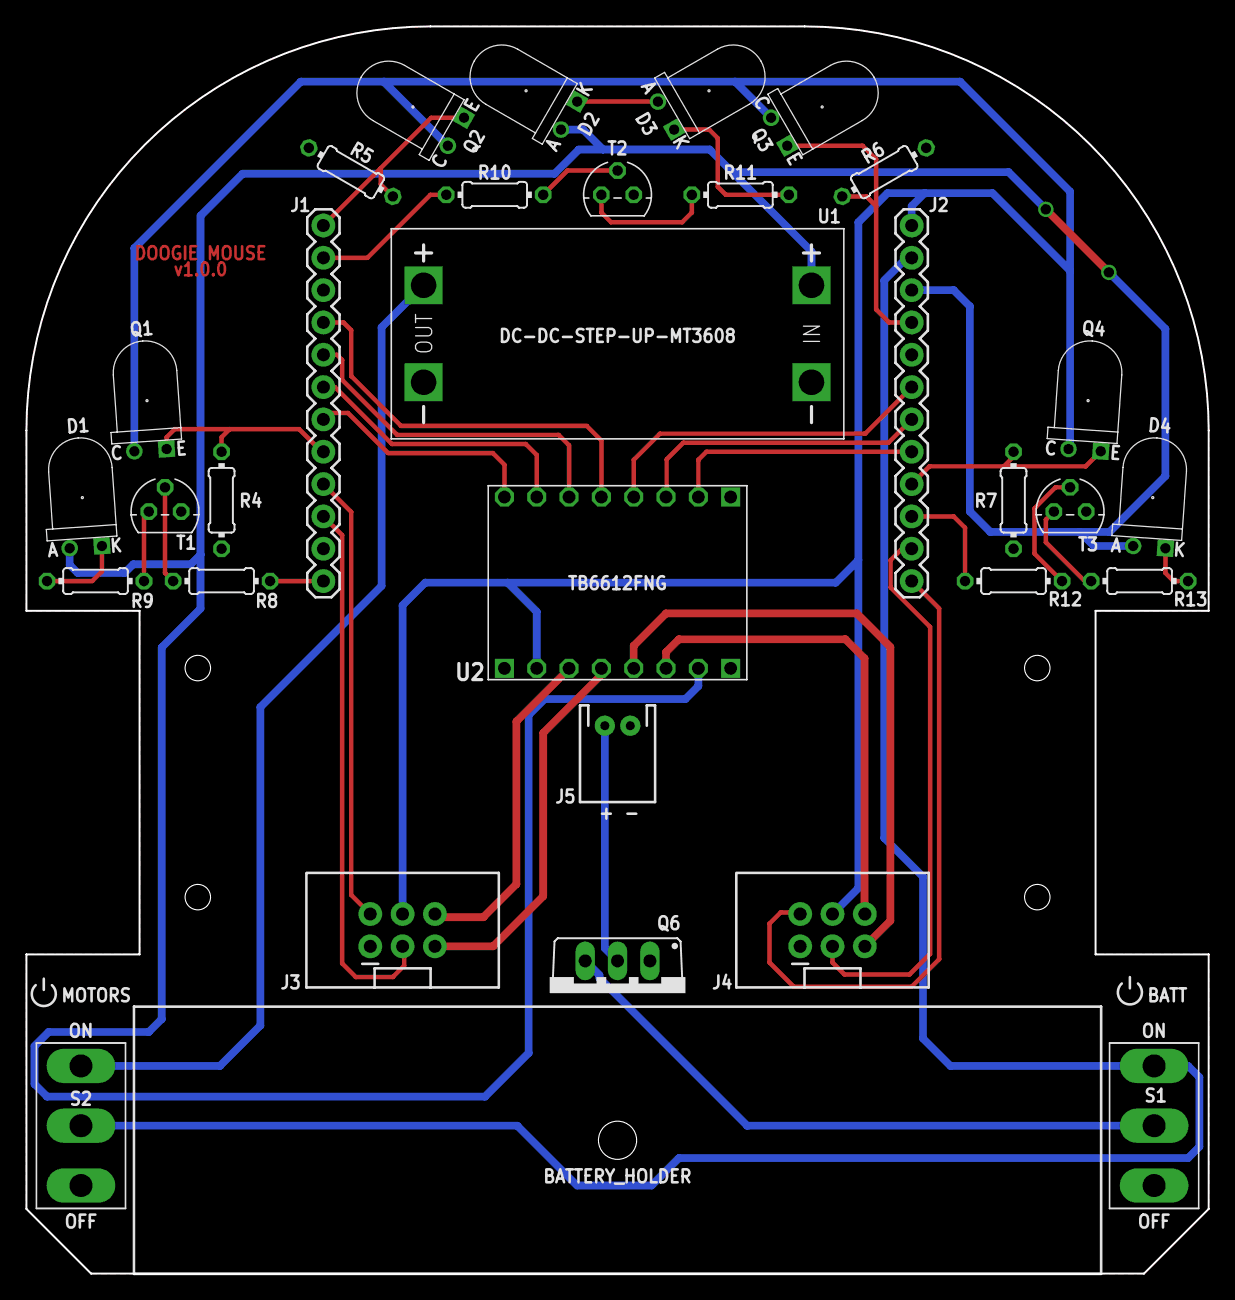
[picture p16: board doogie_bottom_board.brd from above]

Board: 2 copper layers, 92.9 x 98.0 mm, 32 parts (0 on the bottom side), 39 nets.

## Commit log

2019-07-04 Remove unnecessary stuffs
    [doogie_board.brd, doogie_board.sch]
2019-07-17 Add top board
    [doogie_top_board.brd, doogie_top_board.sch]
2019-07-28 Add first version of schematics
    [doogie_bottom_board.brd, doogie_bottom_board.sch, doogie_top_board.brd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]
2019-07-29 Add first version of thebottom board routed
    [doogie_bottom_board.brd]
2019-07-29 Change net order and names
    [doogie_bottom_board.sch]
2019-08-17 Route bottom board
    [doogie_bottom_board.brd, doogie_bottom_board.sch, doogie_top_board.brd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]
2019-08-20 Make top board routing sketch
    [doogie_bottom_board.brd, doogie_top_board.brd, doogie_top_board.sch]
2019-08-22 Add first step of top board routing
    [doogie_top_board.brd, doogie_top_board.sch]
2019-08-24 Add silk
    [doogie_top_board.brd, doogie_top_board.sch]
2019-08-26 Change robot name on silk
    [doogie_bottom_board.brd]
2019-08-26 Add H-bridge name on bottom board silk
    [doogie_bottom_board.brd, doogie_bottom_board.sch]
2019-08-26 Add DC-DC name on silk
    [doogie_bottom_board.brd, doogie_bottom_board.sch]
2019-08-26 Add extra holes on top board
    [doogie_top_board.brd]
2019-08-26 Fiz backanotation error
    [doogie_top_board.sch]
2019-10-01 Fix copper traces of I2C bus
    [doogie_bottom_board.brd, doogie_top_board.brd]
2019-10-01 Add Gerbers and Schematics files
    [doogie_bottom_board.gbl, doogie_bottom_board.gbo, doogie_bottom_board.gtl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]
2019-10-01 Change colors on manufacturing visualization
    [doogie_bottom_board.brd, doogie_top_board.brd]
2019-10-07 Add BIR logo in page frame
    [doogie_bottom_board.sch, doogie_top_board.sch]
2019-10-07 Add dril gerbers files
    [doogie_bottom_board.drl, doogie_top_board.drl]
2019-10-07 Update schematics
2020-03-21 Add Bill Of Materials

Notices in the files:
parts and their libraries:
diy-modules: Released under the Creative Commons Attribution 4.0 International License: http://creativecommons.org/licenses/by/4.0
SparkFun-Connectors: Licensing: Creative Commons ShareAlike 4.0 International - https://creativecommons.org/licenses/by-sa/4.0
